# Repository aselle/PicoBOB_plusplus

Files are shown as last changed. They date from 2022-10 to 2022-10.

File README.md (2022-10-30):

# PicoBOB++ for GRBLHAL and one day LinuxCNC

*This repo is for experimentation. If you want easy nice experience stick with the PicoBOB for now at (https://github.com/Expatria-Technologies/PicoBOB)*

PicoBOB++ is currently an experimental design which is based on Experia's PicoBOB. The primary goals are

The design here is located in PicoBOB_plus_plus and is in KiCad

* Allow using LinuxCNC as well as GrblHal with ideally no rewiring
  * Pins are reassigned to allow SPI to enable LinuxCNC
  * Connects to Raspberry PI via header.
* Use KiCad because I don't have Altium and know hot o use KiCad

Notes

* Unlike PicoBOB RevB, I have gone back to using a Pi Pico devboard. I do not solder with the castellations but use a header placement approach. This simplifies board assembly by hand, and it allows more flexibility to revise while I'm playing with the hardware.
* Uses bigger SMD (0805) and some TH parts currently just because of what I had laying around.
* This is not supported in anyway.
* If you want to have an easy time buy an Experia, see below.

Software

* GrblHal modifications needed for this pinout are in https://github.com/aselle/grblhal-RP2040/tree/picobob_plusplus

Photos

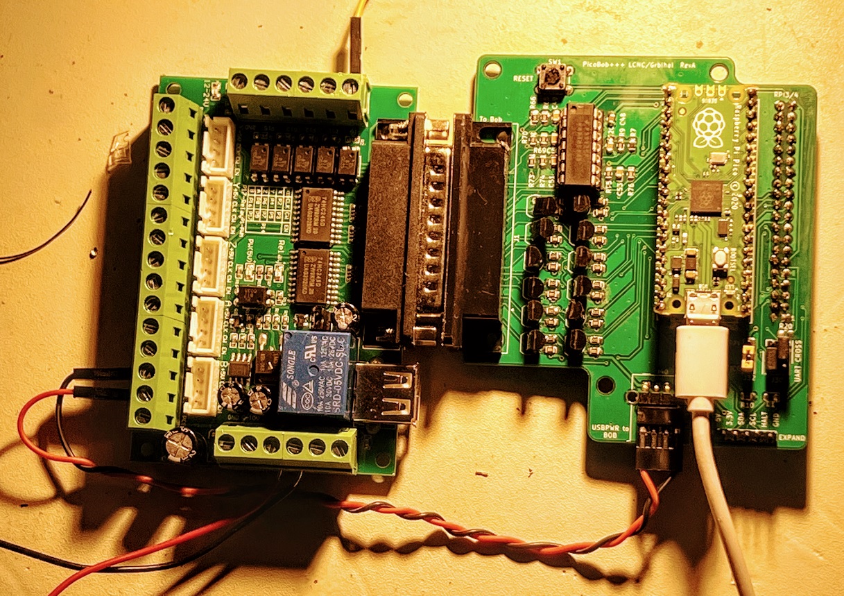
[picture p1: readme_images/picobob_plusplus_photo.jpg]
Photo of PicoBob++

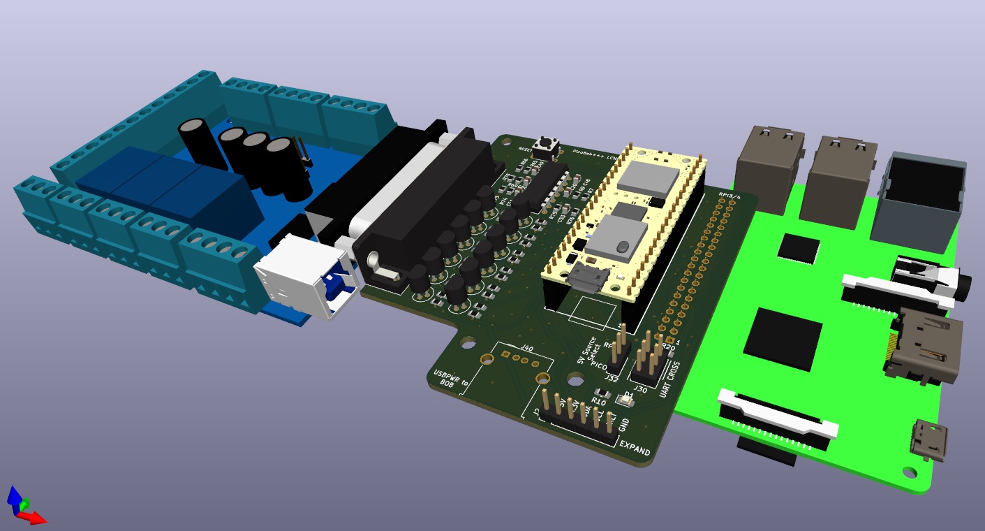
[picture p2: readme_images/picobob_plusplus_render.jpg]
Render of PicoBob++


# PicoBOB for GRBLHAL



Expatria Technologies PicoBOB GRBLHAL module



Currently available in our online store:

https://expatria.myshopify.com/products/picobob

Please consider buying a board to support our open-source designs. 

The PicoBOB allows you to use the high performance GRBLHAL motion control system with a traditional Mach3/LinuxCNC parallel-port breakout board.  It is intended to be simple and low cost.  It uses a Raspberry Pi RP2040 MCU and the widely available 5 axis Mach3 breakout board.  The PicoBOB can be easily sourced from JLCPCB.  The complete BOM and fabrications files are in the CAM_OUTPUTS folder for upload.  The design is free to use by all parties, including commercial parties, under the CERN-OHL-S V2 license.  It is our hope that the community finds the design useful and that it may be carried forward to help advance the PrintNC and broader CNC hobby community.

The PicoBOB closely tracks the features of the Mach3 BOB:

1) Up to 5 axes of step/direction control.
3) 10A Spindle relay control.
4) 0-10V analog spindle speed control.
5) 5 general purpose inputs
6) One general purpose output.

The default GRBLHAL builds for the PicoBOB include the following features that are implemented in the RP2040 port of GRBLHAL:

1) Backlash Compensation.
2) Stress-free Autosquaring for the ganged axis
3) Ganged axis offsets to correct for offset homing switches
4) Step rates tested up to 180 KHz on 5 simultaneous axes.

In addition, the board has a USB micro connector for the 5V that is required for the BOB.  There is also a push button to reset the Pi Pico without disconnecting power.

Gerber output files are in the CAM_OUTPUTS folder, along with BOM and Pick and Place files to facilitate easy ordering from JLCPCB.  Now available as a chip-down design in revision B1.  Older A1 revision for Pi Pico module is still hosted in case you want to do the final soldering by hand.  The two designs are functionally identical.

## PicoBOB Overview



Usage notes:

Communication with GRBLHAL on the PicoBOB is accomplished via the USBC connection on the PicoBOB (not connected in above images).  A short USB cable is used to provide the required 5V for the BOB.  In addition, the BOB requires an external 12-24V supply.

The Mach3 BOB shares the B axis direction signal with a spindle relay enable signal - only one can be used at a time.  Also on the PicoBOB, the stepper enable signal is modified in the GRBLHAL default map file so that it is used as the coolant output signal.  All of this is configurable by re-building the GRBLHAL firwmare.


Above shows the PicoBOB A1 with a Pi Pico installed and connected to the Mach3/LinuxCNC parallel BOB.

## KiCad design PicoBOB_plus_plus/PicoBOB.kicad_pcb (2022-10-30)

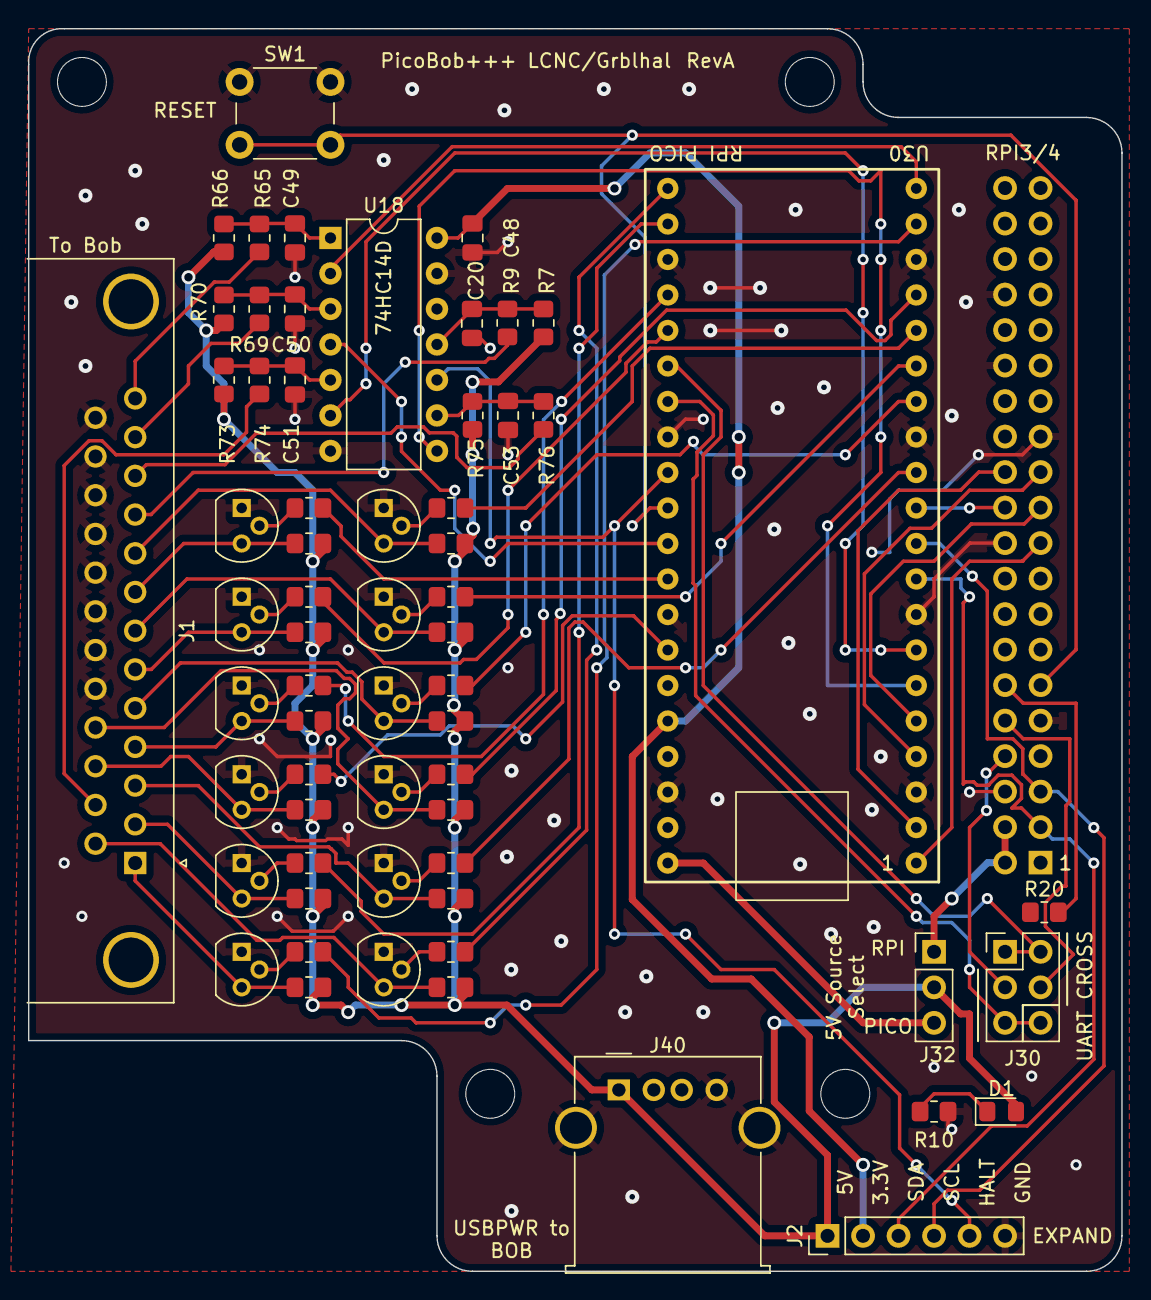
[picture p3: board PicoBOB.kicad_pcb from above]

Board: 2 copper layers, 78.2 x 88.9 mm, 64 parts (1 on the bottom side), 70 nets.

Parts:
C20, C49, C50, C51, C53: 10nF; C_0805_2012Metric_Pad1.18x1.45mm_HandSolder
C48: 1.0uF; C_0805_2012Metric_Pad1.18x1.45mm_HandSolder
D1: LED; LED_0805_2012Metric_Pad1.15x1.40mm_HandSolder
J1: D-DMR025PF-D002; DSUB-25_Female_Horizontal_P2.77x2.84mm_EdgePinOffset4.94mm_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
J2: Conn_01x06_Male; PinHeader_1x06_P2.54mm_Vertical
J30: Conn_02x03_Odd_Even; PinHeader_2x03_P2.54mm_Vertical
J31: Raspberry_Pi_2_3; RaspberryPi
J32: Conn_01x03_Male; PinHeader_1x03_P2.54mm_Vertical
J40: USB_A; USB_A_Molex_67643_Horizontal
Q_Ad_13: 2n3904; TO-92
Q_As_13: 2n3904; TO-92
Q_Bd_13: 2n3904; TO-92
Q_Bs_13: 2n3904; TO-92
Q_EN_13: 2n3904; TO-92
Q_PWM_13: 2n3904; TO-92
Q_Xd_13: 2n3904; TO-92
Q_Xs_13: 2n3904; TO-92
Q_Yd_13: 2n3904; TO-92
Q_Ys_13: 2n3904; TO-92
Q_Zd_13: 2n3904; TO-92
Q_Zs_13: 2n3904; TO-92
R7, R65, R69, R73, R75: 100KΩ ±1%; R_0805_2012Metric_Pad1.20x1.40mm_HandSolder
R9, R66, R70, R74, R76: 510Ω ±1%; R_0805_2012Metric_Pad1.20x1.40mm_HandSolder
R10: 5.1KΩ ±1%; R_0805_2012Metric_Pad1.20x1.40mm_HandSolder
R20: 0; R_0805_2012Metric_Pad1.20x1.40mm_HandSolder
R_Ad_56: 510Ω ±1%; R_0805_2012Metric_Pad1.20x1.40mm_HandSolder
R_Ad_83: 2.2kΩ ±1%; R_0805_2012Metric_Pad1.20x1.40mm_HandSolder
R_As_56: 510Ω ±1%; R_0805_2012Metric_Pad1.20x1.40mm_HandSolder
R_As_83: 2.2kΩ ±1%; R_0805_2012Metric_Pad1.20x1.40mm_HandSolder
R_Bd_56: 510Ω ±1%; R_0805_2012Metric_Pad1.20x1.40mm_HandSolder
R_Bd_83: 2.2kΩ ±1%; R_0805_2012Metric_Pad1.20x1.40mm_HandSolder
R_Bs_56: 510Ω ±1%; R_0805_2012Metric_Pad1.20x1.40mm_HandSolder
R_Bs_83: 2.2kΩ ±1%; R_0805_2012Metric_Pad1.20x1.40mm_HandSolder
R_EN_56: 510Ω ±1%; R_0805_2012Metric_Pad1.20x1.40mm_HandSolder
R_EN_83: 2.2kΩ ±1%; R_0805_2012Metric_Pad1.20x1.40mm_HandSolder
R_PWM_56: 510Ω ±1%; R_0805_2012Metric_Pad1.20x1.40mm_HandSolder
R_PWM_83: 2.2kΩ ±1%; R_0805_2012Metric_Pad1.20x1.40mm_HandSolder
R_Xd_56: 510Ω ±1%; R_0805_2012Metric_Pad1.20x1.40mm_HandSolder
R_Xd_83: 2.2kΩ ±1%; R_0805_2012Metric_Pad1.20x1.40mm_HandSolder
R_Xs_56: 510Ω ±1%; R_0805_2012Metric_Pad1.20x1.40mm_HandSolder
R_Xs_83: 2.2kΩ ±1%; R_0805_2012Metric_Pad1.20x1.40mm_HandSolder
R_Yd_56: 510Ω ±1%; R_0805_2012Metric_Pad1.20x1.40mm_HandSolder
R_Yd_83: 2.2kΩ ±1%; R_0805_2012Metric_Pad1.20x1.40mm_HandSolder
R_Ys_56: 510Ω ±1%; R_0805_2012Metric_Pad1.20x1.40mm_HandSolder
R_Ys_83: 2.2kΩ ±1%; R_0805_2012Metric_Pad1.20x1.40mm_HandSolder
R_Zd_56: 510Ω ±1%; R_0805_2012Metric_Pad1.20x1.40mm_HandSolder
R_Zd_83: 2.2kΩ ±1%; R_0805_2012Metric_Pad1.20x1.40mm_HandSolder
R_Zs_56: 510Ω ±1%; R_0805_2012Metric_Pad1.20x1.40mm_HandSolder
R_Zs_83: 2.2kΩ ±1%; R_0805_2012Metric_Pad1.20x1.40mm_HandSolder
SW1: SKRTLAE010; SW_PUSH_6mm
U18: 74HC14D; DIP-14_W7.62mm
U30: PICO; RPI_PICO

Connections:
+3.3V: C48.1, J2.2, U18.14 (VCC), U30.36 (3v3(out))
+5V: D1.2 (A), J2.1, J32.2, J40.1 (VBUS), R7.2, R65.2, R69.2, R73.2, R75.2, R_Ad_56.2, R_As_56.2, R_Bd_56.2, R_Bs_56.2, R_EN_56.2, R_PWM_56.2, R_Xd_56.2, R_Xs_56.2, R_Yd_56.2, R_Ys_56.2, R_Zd_56.2, R_Zs_56.2
/DIR_A: R_Ad_83.1, U30.16 (GP12)
/DIR_A_5V: J1.9, Q_Ad_13.3 (C), R_Ad_56.1
/DIR_B: R_Bd_83.1, U30.17 (GP13)
/DIR_B_5V: J1.17, Q_Bd_13.3 (C), R_Bd_56.1
/DIR_X: R_Xd_83.1, U30.12 (GP9)
/DIR_X_5V: J1.3, Q_Xd_13.3 (C), R_Xd_56.1
/DIR_Y: R_Yd_83.1, U30.14 (GP10)
/DIR_Y_5V: J1.5, Q_Yd_13.3 (C), R_Yd_56.1
/DIR_Z: R_Zd_83.1, U30.15 (GP11)
/DIR_Z_5V: J1.7, Q_Zd_13.3 (C), R_Zd_56.1
/HALT: J2.5, U18.10 (Y), U30.29 (GP22)
/HALT_5V: J1.10, R9.1
/PICO_5V: J32.3, U30.40 (VBUS)
/PICO_RUN: J31.11 (GPIO17), SW1.2, U30.30 (RUN)
/PROBE: U18.8 (Y), U30.6 (GP4)
/PROBE_5V: J1.11, R76.1
/PRU_RESET: J31.22 (GPIO25), U30.11 (GP8)
/RPI_5V: J31.2 (5V), J31.4 (5V), J32.1
/RXD_INT: J30.5, J30.6, U30.27 (GP21)
/RXD_PI: J30.4, J31.10 (GPIO15/RXD)
/SCL: J2.4, J31.5 (SCL/GPIO3), U30.10 (GP7)
/SDA: J2.3, J31.3 (SDA/GPIO2), U30.9 (GP6)
/SPINDLE_PWM: R_PWM_83.1, U30.19 (GP14)
/SPINDLE_PWM_5V: J1.1, Q_PWM_13.3 (C), R_PWM_56.1
/SPI_CLK: J31.23 (SCLK0/GPIO11), U30.4 (GP2)
/SPI_CS_JOG_SW: J31.24 (~CE0/GPIO8), U30.2 (GP1)
/SPI_MISO: J31.21 (MISO0/GPIO9), U30.5 (GP3)
/SPI_MOSI: J31.19 (MOSI0/GPIO10), U30.1 (GP0)
/STEP_A: R_As_83.1, U30.32 (GP27_A1)
/STEP_A_5V: J1.8, Q_As_13.3 (C), R_As_56.1
/STEP_B: R_Bs_83.1, U30.34 (GP28_A2)
/STEP_B_5V: J1.16, Q_Bs_13.3 (C), R_Bs_56.1
/STEP_X: R_Xs_83.1, U30.22 (GP17)
/STEP_X_5V: J1.2, Q_Xs_13.3 (C), R_Xs_56.1
/STEP_Y: R_Ys_83.1, U30.24 (GP18)
/STEP_Y_5V: J1.4, Q_Ys_13.3 (C), R_Ys_56.1
/STEP_Z: R_Zs_83.1, U30.25 (GP19)
/STEP_Z_5V: J1.6, Q_Zs_13.3 (C), R_Zs_56.1
/STP_EN_XYZAB: R_EN_83.1, U30.21 (GP16)
/STP_EN_XYZAB_5V: J1.14, Q_EN_13.3 (C), R_EN_56.1
/TXD_INT: J30.1, J30.2, U30.26 (GP20)
/TXD_PI: J30.3, J31.8 (GPIO14/TXD)
/X_LIM: U18.4 (Y), U30.31 (GP26_A0)
/X_LIM_5V: J1.12, R70.1
/Y_LIM: U18.2 (Y), U30.20 (GP15)
/Y_LIM_5V: J1.13, R66.1
/Z_LIM: U18.6 (Y), U30.7 (GP5)
/Z_LIM_5V: J1.15, R74.1
GND: C20.1, C48.2, C49.1, C50.1, C51.1, C53.1, J1.18, J1.19, J1.20, J1.21, J1.22, J1.23, J1.24, J1.25, J2.6, J31.6 (GND), J31.9 (GND), J31.14 (GND), J31.20 (GND), J31.25 (GND), J31.30 (GND), J31.34 (GND), J31.39 (GND), J40.4 (GND), J40.5 (Shield), Q_Ad_13.1 (E), Q_As_13.1 (E), Q_Bd_13.1 (E), Q_Bs_13.1 (E), Q_EN_13.1 (E), Q_PWM_13.1 (E), Q_Xd_13.1 (E), Q_Xs_13.1 (E), Q_Yd_13.1 (E), Q_Ys_13.1 (E), Q_Zd_13.1 (E), Q_Zs_13.1 (E), R10.2, SW1.1, U18.7 (GND), U18.13 (A), U30.3 (GND_1), U30.8 (GND_2), U30.13 (GND_3), U30.18 (GND_4), U30.23 (GND_5), U30.28 (GND_6), U30.33 (GND_7), U30.38 (GND_8)
unnamed: C20.2, R7.1, R9.2, U18.11 (A)
unnamed: C49.2, R65.1, R66.2, U18.1 (A)
unnamed: C50.2, R69.1, R70.2, U18.3 (A)
unnamed: C51.2, R73.1, R74.2, U18.5 (A)
unnamed: C53.2, R75.1, R76.2, U18.9 (A)
unnamed: D1.1 (K), R10.1
unnamed: J31.12 (GPIO18/PWM0), R20.2
unnamed: Q_Ad_13.2 (B), R_Ad_83.2
unnamed: Q_As_13.2 (B), R_As_83.2
unnamed: Q_Bd_13.2 (B), R_Bd_83.2
unnamed: Q_Bs_13.2 (B), R_Bs_83.2
unnamed: Q_EN_13.2 (B), R_EN_83.2
unnamed: Q_PWM_13.2 (B), R_PWM_83.2
unnamed: Q_Xd_13.2 (B), R_Xd_83.2
unnamed: Q_Xs_13.2 (B), R_Xs_83.2
unnamed: Q_Yd_13.2 (B), R_Yd_83.2
unnamed: Q_Ys_13.2 (B), R_Ys_83.2
unnamed: Q_Zd_13.2 (B), R_Zd_83.2
unnamed: Q_Zs_13.2 (B), R_Zs_83.2

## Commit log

2022-10-30 PicoBOB++ Experimental Board using Kicad Based on PicoBOB
    * Make kicad board
    * Remap pins to allow SPI
    * Relayout with larger smd parts
    * Add expansion i2c header
    * Add Header for Mounting Pico board
    * Add Header for Mounting RPI 3b or 4
    [5V_Output_shift.kicad_sch, PWR.kicad_sch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]
2022-10-30 Edit Readme and add images
    * Add another note to the README about not using inline rp2040
    and instead go to using RPI Pico
    * Add imagery

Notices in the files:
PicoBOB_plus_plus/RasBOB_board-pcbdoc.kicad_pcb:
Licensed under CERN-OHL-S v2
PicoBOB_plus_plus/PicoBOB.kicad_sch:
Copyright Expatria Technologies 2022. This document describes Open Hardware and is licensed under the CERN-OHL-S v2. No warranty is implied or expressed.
